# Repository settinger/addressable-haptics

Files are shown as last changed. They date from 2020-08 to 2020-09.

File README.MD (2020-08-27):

# Addressable Haptics

This project aims to make it easy to control long strings of haptic motors (or regular motors, or just about anything) from an Arduino or similar microcontroller. By decentralizing the motor control systems, daisy-chaining the motors and relying on one-wire communication, we drastically cut down on the number of PWM output pins needed.

This project and README are works-in-progress. Expect lots of changes.

## About the circuit

Each motor is accompanied by an ATtiny10 microcontroller that handles the reception, transmission, and decoding of commands. When a valid command is read, the ATtiny10 sets the motor intensity by PWMing an N-channel MOSFET. The ATtiny10 will continue to drive the motor while receiving and transmitting additional commands.

## About the communication protocol

Each chain of motors communicates using one wire, similar to the WS2812 LED system. Unlike the WS2812 LEDs, these motors are controlled individually, without a shift register. I felt that a shift register protocol would not be as useful for haptic motor applications, so I did not implement it.

The coding scheme is simple but I don't know the name for it. A one bit is encoded as LOW for 20 μs, then HIGH for 180 μs. A zero bit is encoded as LOW for 150 μs, then HIGH for 50 μs. When not transferring information, the line is usually HIGH. The actual timing of the bits may change as I continue development, so watch out!

Motors are given unary addresses. The first motor is address _0_, the second is address _10_, the third is _110_, the fourth is _1110_, the _n_th is (_n_-1) 1s followed by a 0. This allows the motor controllers to pass commands down the chain with less latency; however, it creates a strong disincentive for long chains of motors.

Each command is of the form `<address><value>`. The `value` is a 7-bit number that sets the PWM duty cycle for the motor at `address`. So, for example, the command `11101010101` would set motor #4 (that is, the motor with address `1110`) to an intensity of `1010101`, or 85/127.

## Some more detail about the communication protocol

If the first ATtiny10 receives a command that starts with `0`, it knows instantly that the message is intended for it. Similarly, if the first ATtiny10 receives a command that starts with `1`, it knows to pass the message down the line. However, it transmits the message _without the initial bit_. That is, if an ATtiny10 receives the command `101111111`, it would pass along the message `01111111`. This informs the next ATtiny10 in the chain that the command is intended for it.

## Why not just use WS2811 ICs?

1. I wanted to implement my own protocol and learn from the process.
1. I don't know the PWM frequency of the WS2811 and can't change it to suit inductive loads.
1. The shift-register approach doesn't make sense for the applications I envision.
1. I just enjoy using ATtiny10s!

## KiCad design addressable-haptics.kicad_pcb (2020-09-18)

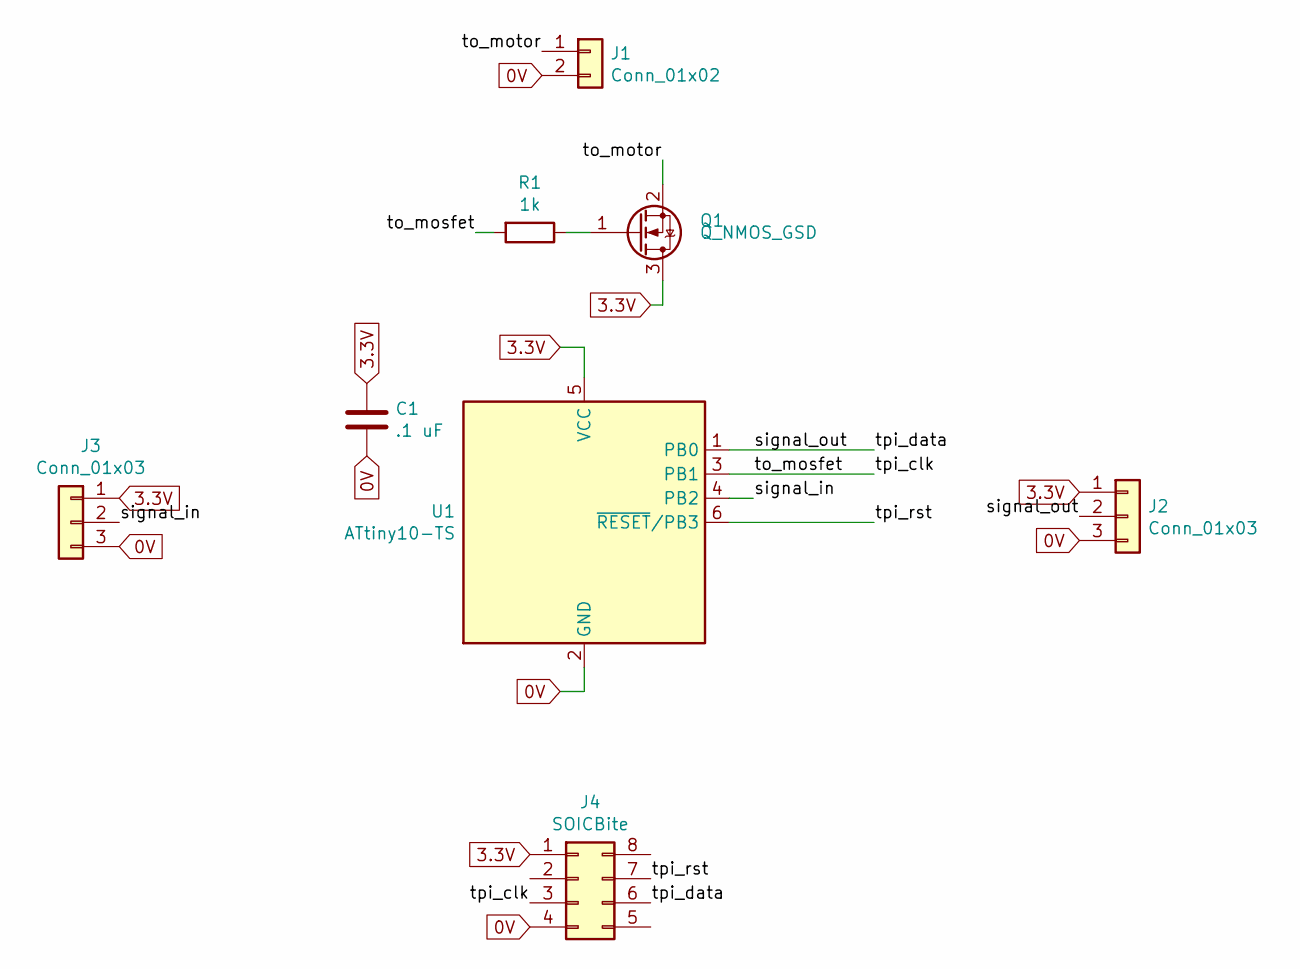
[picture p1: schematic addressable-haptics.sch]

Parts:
C1: .1 uF; C_0805_2012Metric
J1: Conn_01x02; PinSocket_1x02_P2.54mm_Vertical
J2: Conn_01x03; PinSocket_1x03_P2.54mm_Horizontal
J3: Conn_01x03; PinHeader_1x03_P2.54mm_Horizontal
J4: SOICBite; SOIC_clipProgSmall
Q1: Q_NMOS_GSD; SOT-23
R1: 1k; R_0805_2012Metric
U1: ATtiny10-TS; SOT-23-6

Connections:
0V: C1.2, J1.2, J2.3, J3.3, J4.4, U1.2 (GND)
3.3V: C1.1, J2.1, J3.1, J4.1, Q1.3 (D), U1.5 (VCC)
/signal_in: J3.2, U1.4 (PB2)
/signal_out: J2.2, J4.6, U1.1 (PB0)
/to_mosfet: J4.3, R1.2, U1.3 (PB1)
/to_motor: J1.1, Q1.2 (S)
/tpi_rst: J4.7, U1.6 (~RESET~/PB3)
unnamed: Q1.1 (G), R1.1

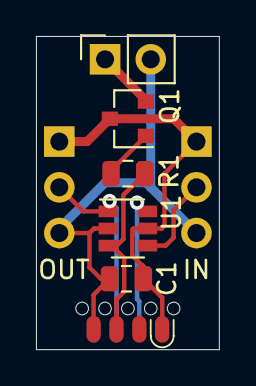
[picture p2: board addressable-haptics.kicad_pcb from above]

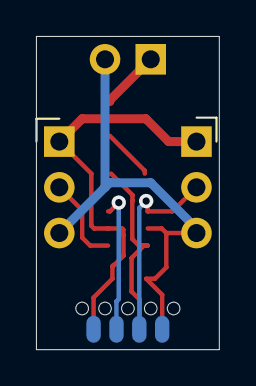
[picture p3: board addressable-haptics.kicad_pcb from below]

Board: 2 copper layers, 10.2 x 17.4 mm, 8 parts (2 on the bottom side), 8 nets.

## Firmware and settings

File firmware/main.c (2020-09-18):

#define F_CPU 8000000UL
#include <avr/io.h>
#include <util/delay.h>
#include <avr/interrupt.h>

// Variables used below
volatile int timeSinceLastSignal = 0; // Approx. number of milliseconds without receiving a valid signal
int mode = 0;                 // 0: idle mode; 1: pass-through mode; 2: receiver mode
char receivedBit = 0x00;      // What value to transmit when in pass-through mode
int bitsReceived = 0;         // How many bits received in receiver mode
int receivedData = 0;         // Data obtained in receiver mode
volatile int interrupted = 0; // If the interrupt flag is set

void Setup(void) {
  CCP = 0xD8;             // Unlock clock prescaler register
  CLKPSR = 0b0000;        // Set clock to 8 MHz
  
  TCCR0A = (3<<COM0B0) | (2<<WGM00); // Datasheet p100; set PB1 (Pin 3) as PWM pin
  TCCR0B = (3<<WGM02) | (2<<CS00);   // Datasheet p103; set PWM behavior, set clock scaler to 1 MHz
  OCR0B = 1023;                      // Counter for PWM on PB1 (pin 3)
  ICR0 = 1023;                       // Counter resets approx. every millisecond, good for timing
  OCR0A = 511;                       // A nice middle-of-the-range value for timing during PWM
  DDRB = 3<<PORTB0;                  // Datasheet p76; Set PB1 (pin 3) and PB0 (pin 1) as output
  PUEB = 4<<PUEB0;                   // Datasheet p74; set PB2 (pin 4) to use internal pullup resistor
  sei();                             // Datasheet p25; enable interrupts
  EIMSK = 1;                         // Datasheet p57; enable external interrupts
  EICRA |= 2<<ISC00;                 // Datasheet p56; set external interrupt to detect falling edge
}

void idleMode(void) {
  mode = 0;
  timeSinceLastSignal = 0;
  bitsReceived = 0;
  receivedBit = 0;
  receivedData = 0;
}

void passThroughMode(void) {
  mode = 1;
  timeSinceLastSignal = 0;
  bitsReceived = 0;
  receivedBit = 0;
  receivedData = 0;
}

void receiverMode(void) {
  mode = 2;
}

void sendSignal(char signal) {
  // If signal is a logical 1: clear PORTB0 for 20 μs, set PORTB0 for 80 μs, exit
  // If signal is a logical 0: clear PORTB0 for 80 μs, set PORTB0 for 20 μs, exit
  if (signal) {
    PORTB &= 0b1110;
    _delay_us(20);
    PORTB |= 0b0001;
    _delay_us(80);
    } else {
    PORTB &= 0b1110;
    _delay_us(80);
    PORTB |= 0b0001;
    _delay_us(20);
  }
}

// Check if a falling edge was detected on Pin 4
ISR(INT0_vect) {
  interrupted = 1;
}

int main(void) {
  
  Setup();
  
  while(1) {
    // Check if PB2 (pin 4) has triggered an interrupt
    if (interrupted) {
      interrupted = 0; // Clear interrupt flag
      timeSinceLastSignal = 0; // Clear idle timer
      // Wait .04 ms, take reading
      _delay_us(40);
      receivedBit = PINB & 0b00000100;
      
      // If we're in idle mode and reading is HIGH: enter pass-through mode
      if (mode == 0 && receivedBit) {
        passThroughMode();
      }
      // If we're in idle mode and reading is LOW: enter receiver mode
      else if (mode == 0 && !receivedBit) {
        receiverMode();
      }
      // If we're in pass-through mode: pass through
      else if (mode == 1) {
        sendSignal(receivedBit);
      }
      // If we're in receiver mode: add bit to received byte
      else if (mode == 2) {
        if (receivedBit) {
          receivedData |= 1<<bitsReceived;
        }
        bitsReceived++;
        // If we've received seven bits: set OCR0B to the new motor intensity and enter idle mode
        if (bitsReceived >= 7) {
          OCR0B = 8*receivedData;
          idleMode();
        }
      }
    }
    
    // Check if OC0A has ticked over
    if (TIFR0 & (1<<OCF0A)) {
      timeSinceLastSignal++;
      TIFR0 |= 1<<OCF0B; // Clear interrupt flag by writing a 1 to the register
    }
    
    // If we've been idle for approx. 5 milliseconds, enter idle mode
    if (timeSinceLastSignal >= 3) {
      idleMode();
    }
  }
}

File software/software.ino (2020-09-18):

// Arduino code to drive a daisy-chained series of addressable haptic motors

#define datapin 8

// Send a manchester-encoded high bit
// Low for 20 microseconds, high for 280 microseconds
void sendHigh(void) {
  digitalWrite(datapin, LOW);
  delayMicroseconds(20);
  digitalWrite(datapin, HIGH);
  delayMicroseconds(120);
}

// Send a manchester-encoded low bit
// Drive pin low for 250 microseconds, high for 50 microseconds
void sendLow(void) {
  digitalWrite(datapin, LOW);
  delayMicroseconds(120);
  digitalWrite(datapin, HIGH);
  delayMicroseconds(20);
}

// Set the intensity of one motor
void setValue(int address, int value) {
  // First, send the address
  // If the haptic motor is at address n, send n manchester-encoded 1's then a zero
  for (int i=0; i<address; i++) {
    sendHigh();
  }
  sendLow();

  // Next, send the seven-bit intensity
  int bitToSend;
  for (int i=0; i<7; i++) {
    bitToSend = value & 1<<i;
    bitToSend ? sendHigh() : sendLow();
  }
}

void setup() {
  // put your setup code here, to run once:
  pinMode(datapin, OUTPUT);
  digitalWrite(datapin, HIGH);
  delay(1000);
  setValue(3, 127);
  delay(1000);
  setValue(2, 127);
  delay(1000);
  setValue(1, 127);
  delay(1000);
  setValue(0, 127);
  delay(1000);
  setValue(3, 0);
  delay(1000);
  setValue(2, 0);
  delay(1000);
  setValue(1, 0);
  delay(1000);
  setValue(0, 0);
  delay(1000);
}

void loop() {
  // put your main code here, to run repeatedly:
  for (signed int i=0; i<64; i++) {
    setValue(0, 2*i);
    delay(4);
    setValue(1, 127-2*i);
    delay(4);
    setValue(2, 2*i);
    delay(4);
    setValue(3, 127-2*i);
    delay(4);
  }
  for (signed int i=0; i<64; i++) {
    setValue(0, 127-2*i);
    delay(4);
    setValue(1, 2*i);
    delay(4);
    setValue(2, 127-2*i);
    delay(4);
    setValue(3, 2*i);
    delay(4);
  }
}

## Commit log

2020-02-19 Fixed interrupt startup
2020-08-19 Updates now that I have hardware to test
    [addressable-haptics.kicad_pcb]
2020-08-21 Updated firmware and software
    [addressable-haptics.sch]
2020-08-21 Update PCB
    [addressable-haptics.kicad_pcb, addressable-haptics.sch]
2020-08-27 Fixed schematic
    [addressable-haptics.kicad_pcb, addressable-haptics.sch]
2020-09-18 Sped up instructions
    [addressable-haptics.kicad_pcb]
